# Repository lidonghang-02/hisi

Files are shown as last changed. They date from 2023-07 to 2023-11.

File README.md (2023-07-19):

# **猫咪自动铲屎机**
---
# 主体结构设计

主要分为三大部分，物联网部分、外壳设计、功能设计。

## 功能设计

不同于传统旋转式猫咪铲屎机，我们大胆采用了直线式铲屎。传统猫咪铲屎机，为旋转式铲屎，利用滚筒和网筛选出猫砂，再让猫屎自由落体进入容器中。这种结构可以说相当精妙，但这也使得清洁和处理猫砂成为一个问题。使得这种自动成为另一种负担。

而直线式可以有效解决这一问题。正如远距离传电由交流转为直流一般，大道至简。直线式，可将底部容器分为两个部分，一个装排泄物，一个装废弃的猫砂。并且可以方便的套上垃圾袋，方便铲屎官。

直线式并非完美无缺，这对于电机扭矩有极大的要求。因此我们特意选择了步进电机作为驱动装置，并且配合限位开关来限制步进电机的移动距离。然而这带来了另一个问题，即速度慢。经过我们深入研究Hi3861的硬件，我们选择Hi3861的硬件定时器，基于寄存器与内核代码重构硬件定时器代码，实现了us级脉冲，以此来驱动步进电机的高速运转。并且将其完善，使得其可以同STM32般简单易用，大大方便后续开发者，我们将其命名为“EasyTimer”。

当然，对于猫咪铲屎机，防夹猫也是一项必不可少的功能。每个铲屎官都害怕铲屎机会对可爱的猫主子造成伤害。因此，我们使用超声波测距来检测猫主子，当超声波的检测距离小于事先设定的阈值时，说明猫咪在铲屎机中;反之，则猫咪不在。

同时，超声波检测的距离变化也是我们铲屎的信号之一，其与压力模块的检测数据相结合来构成我们的铲屎信号。 我们通过测定重量的变化值来确定设备的工作状态以及排泄物重量。

对于一个设备没有UI是万万不可的，因此我使用OLED显示一些相关信息，供铲屎官了解。

此外，为了方便铲屎官对猫咪自动铲屎机的使用，我们开发了一个APP来实时监测猫咪自动铲屎机的工作状态和相关信息，让铲屎官在手机上就可以操控铲屎机。

## 物联网
在物联网方面，我们使用了华为云的IoT物联网中的设备接入IoTDA。通过MQTT协议与华为云IoT连接，并实时上传剩余猫砂重量，铲掉的排泄物重量等信息。

此外，我们开发了一个APP通过华为云IoT的API读取上传的数据，来实时监控铲屎机的工作状况和信息，并且可以通过发送指令，来控制铲屎机。该APP连接华为云，设备则通过MQTT连接华为云，实时发送数据和接受指令，并执行指令。

同时我们设计wifi配网功能，在启动时会自动读取nv工厂区的wifi配置，如果没有发现wifi，则进入AP配网模式。手机连接设备的热点后，发送wifi的ssid和密码即可配网。配网后会自动将相关配置写入nv工厂区，在下次启动时便会自动调用。

## 外壳设计



在外壳设计方面，我们始终贯彻方便铲屎官的理念。我们将铲屎机分为上下两个部分，上下都可拆卸，方便清洗。下面为分离的容器，上面则为猫砂盆，负责铲屎。



由于各种因素的影响，铲屎机的外壳对我们来说并不容易制造，因此我们仅在视频中展示了不成熟的结构演示。

与视频不同的是，我们将重力测量模块移到铲屎机的中部，位于猫砂盆底座的总部，并通过滑槽与滑块实现了猫砂盆底座与猫砂盆的分离与结合。为防止其意外脱落，我们还通过多种方式固定猫砂盆，但拆卸下来仅需四五步，十分方便。



更多的外壳细节，请自行查看3D模型。为方便查看，我们已经将其半剖视图制成PDF文件，并把各个部件导出为STL文件。

# 任务调度设计


众所周知HI3861是搭载有liteos的，因此为了压榨Hi3861的性能以及充分利用系统资源，我们抛弃了裸机定时器处理不同任务的方式，详细设计了任务调度。优先级从高到低分别为：电机驱动、传感器、按键检测、数据发送。其中电机为硬件定时器驱动的，因此在此不过多讨论。

裸机最大的问题就是单线程处理任务，因此在一些中大型项目甚至一些小型项目中会出现任务阻塞。导致整个设备运行阻塞，甚至瘫痪。我们便针对这种情况，不断进行设计和调试，便形成了如上图的任务调度。

传感器是防夹猫的关键，为保证猫主子的安全，我们将其置于优先级第一位。按键检测，对于时序要求也是相当高的，因此我们置于第二位，数据接受则置于最后。

# 功能说明

## UI界面显示

在OLED上，我们总共显示了三个参数，分别是：剩余猫砂重量、铲屎重量、铲屎次数。通过这三个参数，铲屎官可以了解猫咪的排泄状况以及添加猫砂的时间。

## 按键操作

为了方便操作，我们同时还设计了按键系统，通过按键的单击、双击、三击、长按，即可操控设备的运转。

长按是进入配网模式，如果已经连接wifi则不会进入。

双击是重新初始化重力感应模块，这需要在没有猫砂的时候进行，这样可以消除误差。

三击，打开舵机，使猫砂流入下方容器，方便更换猫砂。

## APP

可以远程监控设备数据，包括：铲屎重量，以及剩余猫砂重量。

同时配备铲屎的指令，一键即可开始工作。

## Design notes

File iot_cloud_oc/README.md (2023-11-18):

# 使用华为云IOT平台，代码依据使用BearPi-HM_Nano开发板智慧农业案例修改

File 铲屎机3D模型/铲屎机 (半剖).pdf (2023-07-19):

setPageBoxes("Crop", 0, 0, [0,2000,2000,0]);
标题零件代号 | 铲屎机 修订号 设计者 | Selcon 工程师 注释

本文档中的信息和/或材料均属作者所有，具有机密性。未经 书面授权，任何人不得使用、转载、出版或公开这些信息。 这些信息只能用于本文档中指定的制造业项目。

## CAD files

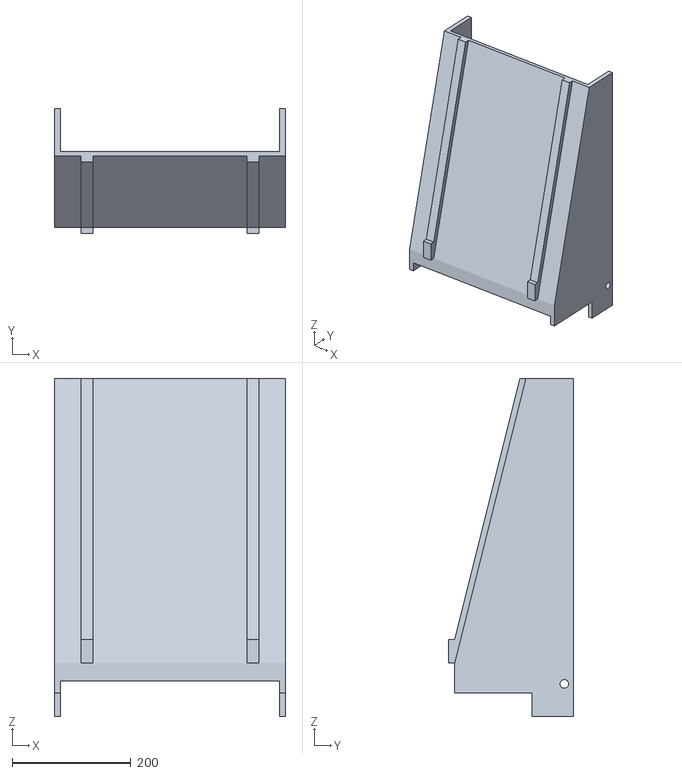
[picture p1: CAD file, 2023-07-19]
铲屎机3D模型/STL/猫砂盆.stl
390.0 x 210.0 x 570.0

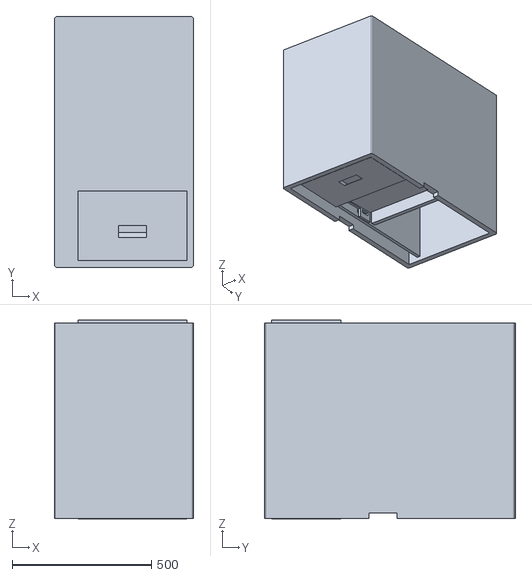
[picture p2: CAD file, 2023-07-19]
铲屎机3D模型/STL/铲屎机.stl
500.0 x 900.0 x 712.0

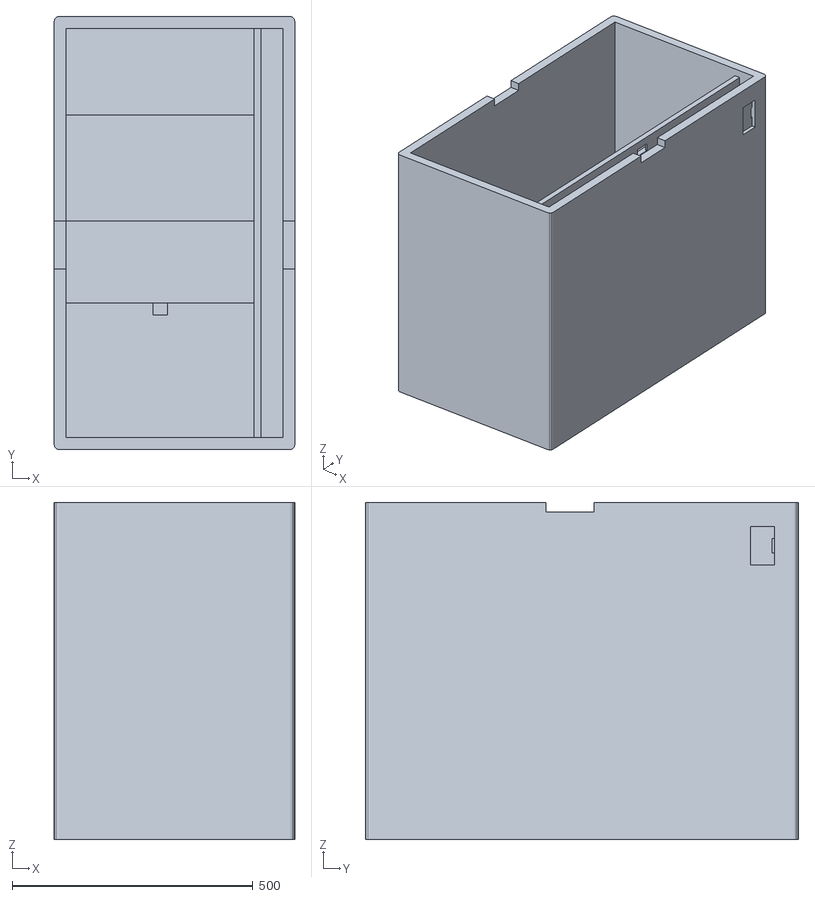
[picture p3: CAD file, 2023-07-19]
铲屎机3D模型/STL/外壳.stl
500.0 x 900.0 x 700.0

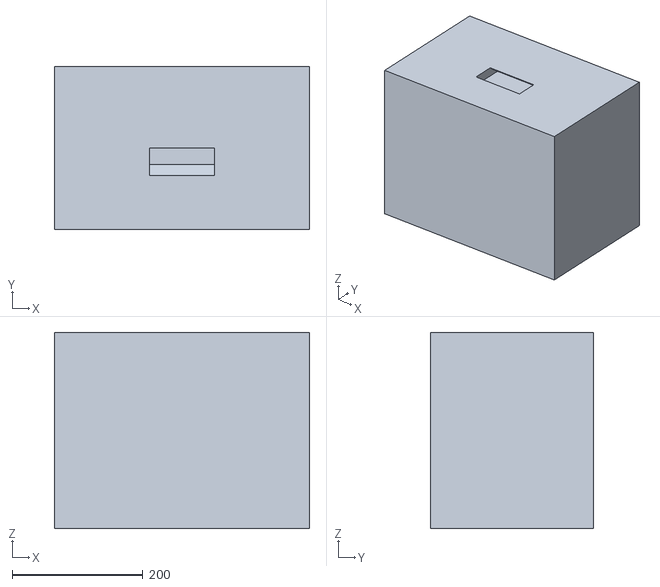
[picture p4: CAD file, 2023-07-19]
铲屎机3D模型/STL/容器.stl
390.0 x 250.0 x 300.0

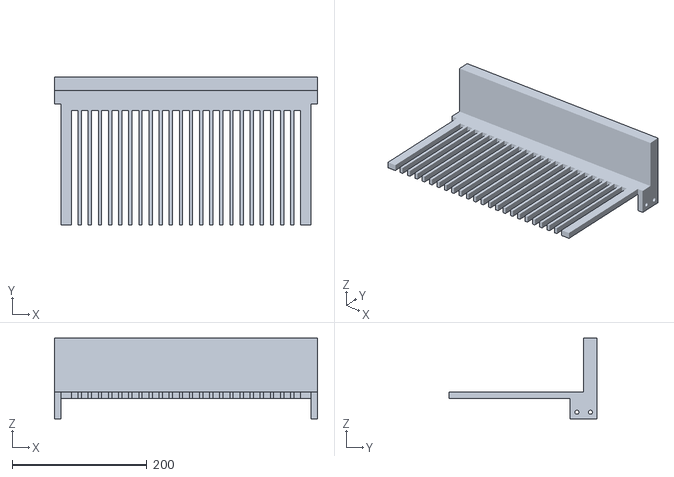
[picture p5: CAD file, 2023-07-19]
铲屎机3D模型/STL/猫铲.stl
390.0 x 220.0 x 120.0

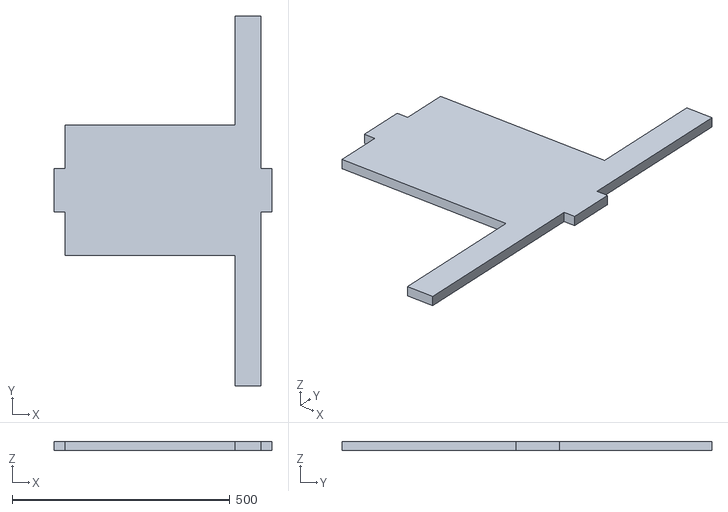
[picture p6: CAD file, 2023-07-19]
铲屎机3D模型/STL/外壳挡板.stl
500.0 x 850.0 x 20.0

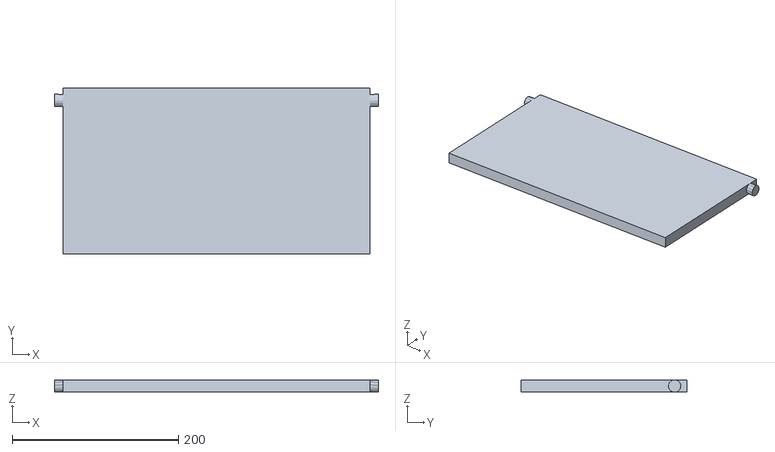
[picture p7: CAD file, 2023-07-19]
铲屎机3D模型/STL/挡板.stl
390.0 x 200.0 x 15.0

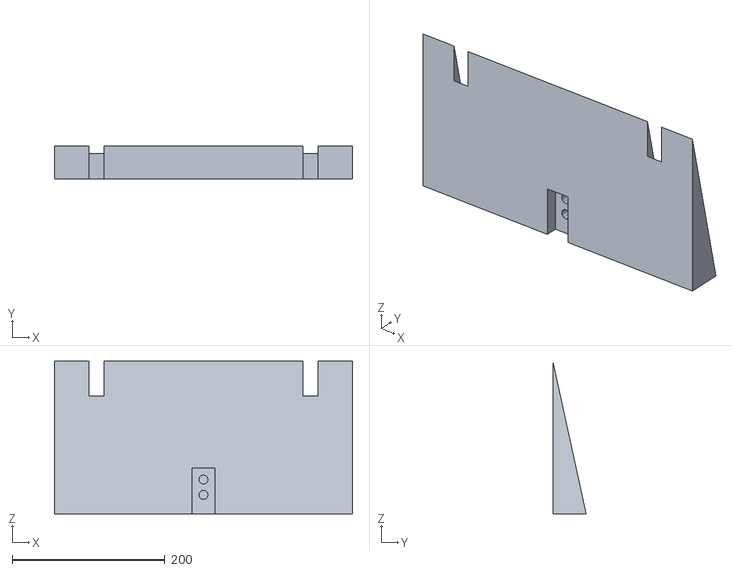
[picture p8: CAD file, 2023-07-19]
铲屎机3D模型/STL/猫砂盆底座.stl
390.0 x 43.6 x 200.0

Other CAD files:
铲屎机3D模型/外壳.ipt
铲屎机3D模型/外壳挡板.ipt
铲屎机3D模型/容器.ipt
铲屎机3D模型/挡板.ipt
铲屎机3D模型/猫砂盆.ipt
铲屎机3D模型/猫砂盆底座.ipt
铲屎机3D模型/猫铲.ipt
铲屎机3D模型/铲屎机.iam

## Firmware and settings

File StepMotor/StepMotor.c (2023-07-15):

#include "StepMotor.h"
#include "EasyTimer.h"
#include "EasyIsr.h"
#include "cmsis_os2.h"
#include <stdlib.h>
#include "LitterCleaner.h"

// #define Speed_Max

osTimerId_t Timer_ID = 0;
int8_t direction = 0;
Typedef_EasyTimerInit StepMotor_Timer = {0};
Typedef_EasyIsrInit StepMotor_Isr = {0};

/**
 * @brief 初始化电机IO口
 *
 * @param StepMotor_Pin 所要初始化的IO
 */
void StepMotor_InitPin(uint8_t StepMotor_Pin, uint8_t StepMotor_PinFunc)
{
    IoTGpioInit(StepMotor_Pin);
    IoTGpioSetFunc(StepMotor_Pin, StepMotor_PinFunc);
    IoTGpioSetDir(StepMotor_Pin, IOT_GPIO_DIR_OUT);
}

void StepMotor_CallbackFunc(void)
{
    static int8_t count = 0;

    StepMotor_SetStatus(count);

    if (direction == Positive)
    {
        if (++count >= 8)
            count = 0;
    }
    else if (direction == Negative)
    {
        if (--count < 0)
            count = 7;
    }

    // printf("Get into the IT, count = %d\n", count);
    EasyTimer_ClearIsrFlag(&StepMotor_Timer);
}

// void StepMotor_ControlCallbackFunc(void)
// {
// }

void StepMotor_PinInit(void)
{
    // Gpio set high level
    StepMotorPin_OFF;

    // Init Gpio
    StepMotor_InitPin(StepMotor_PinA, StepMotor_PinAFunc);
    StepMotor_InitPin(StepMotor_PinB, StepMotor_PinBFunc);
    StepMotor_InitPin(StepMotor_PinC, StepMotor_PinCFunc);
    StepMotor_InitPin(StepMotor_PinD, StepMotor_PinDFunc);
}

void StepMotor_PinDeInit(void)
{
    StepMotorPin_ON;
    IoTGpioDeinit(StepMotor_PinA);
    IoTGpioDeinit(StepMotor_PinB);
    IoTGpioDeinit(StepMotor_PinC);
    IoTGpioDeinit(StepMotor_PinD);
    
}

/**
 * @brief 电机初始化，包括IO和定时器
 *
 */
void StepMotor_Init(void)
{
    // initialize hardware timer to control the operation of step motor
    StepMotor_Timer.DEVICE = TIMER2;
    StepMotor_Timer.ITMASK = ITMASK_DISABLE;
    StepMotor_Timer.LOAD = EasyTimer_GetClockFreq();
    StepMotor_Timer.MODE = MODE_CYCLE;
    StepMotor_Timer.NVIC = NVIC_DISABLE;

    EasyHi_Error ack = EasyTimer_Init(&StepMotor_Timer);
    if (ack != EasyHi_SUCCESS)
        printf("Timer Error:%d\n", ack);
    else
        printf("StepMotor Timer Init Successfully!\n");

    // initialize the interrupt of hardware timer
    StepMotor_Isr.CALLBACKFUNC = StepMotor_CallbackFunc;
    StepMotor_Isr.CALLBACKPARA = NULL;
    StepMotor_Isr.DEVICE = TIMER_2_IRQ;
    StepMotor_Isr.PRIORITY = 7;

    ack = EasyIsr_Init(&StepMotor_Isr);
    if (ack != EasyHi_SUCCESS)
        printf("Isr Error:%d\n", ack);
    else
        printf("StepMotor Isr Init Successfully!\n");

    // // initialize the osTimer to control the speed of step motor
    // Timer_ID = osTimerNew(StepMotor_ControlCallbackFunc, osTimerPeriodic, NULL, NULL);
    // if (Timer_ID == NULL)
    //     printf("osTimer Init Fail\n");
    // else
    //     printf("osTimer Init Successfully\n");
}

void StepMotor_SetStatus(uint8_t motor_status)
{
    switch (motor_status)
    {
    case 0:
        StepMotorPin_OFF;
        StepMotorPinA_ON;
        break;
    case 1:
        StepMotorPin_OFF;
        StepMotorPinA_ON;
        StepMotorPinB_ON;
        break;
    case 2:
        StepMotorPin_OFF;
        StepMotorPinB_ON;
        break;
    case 3:
        StepMotorPin_OFF;
        StepMotorPinB_ON;
        StepMotorPinC_ON;
        break;
    case 4:
        StepMotorPin_OFF;
        StepMotorPinC_ON;
        break;
    case 5:
        StepMotorPin_OFF;
        StepMotorPinC_ON;
        StepMotorPinD_ON;
        break;
    case 6:
        StepMotorPin_OFF;
        StepMotorPinD_ON;
        break;
    case 7:
        StepMotorPin_OFF;
        StepMotorPinD_ON;
        StepMotorPinA_ON;
        break;
    default:
        printf("[StepMotor]Wrong Status!\n");
        break;
    }
    // printf("StepMotor_Status = %d\n", motor_status);
}

void StepMotor_SetSpeed(uint32_t cycle, int8_t direct)
{
    StepMotor_Timer.LOAD = cycle;
    EasyTimer_SetLoad(&StepMotor_Timer);
    direction = direct;
}

void StepMotor_Run(MotorStatus status)
{
    switch (status)
    {
    case FOR:
        osTimerStop(KeyTimer_ID);
        StepMotor_PinInit();
        StepMotor_SetSpeed(40000, Positive);
        EasyTimer_Start(&StepMotor_Timer);
        EasyIsr_Start(&StepMotor_Isr);
        printf("Motor Run Positive\n");
        break;
    case REW:
        StepMotor_SetSpeed(40000, Negative);
        EasyTimer_Start(&StepMotor_Timer);
        EasyIsr_Start(&StepMotor_Isr);
        printf("Motor Run Negative\n");
        break;
    case OFF:
        StepMotor_PinDeInit();
        EasyIsr_Stop(&StepMotor_Isr);
        EasyTimer_Stop(&StepMotor_Timer);
        Key_PinInit();
        osTimerStart(KeyTimer_ID, 1);
        printf("OFF\n");
        break;
    default:
        break;
    }
}

void StepMotor_Test(void)
{
    if (EasyTimer_Start(&StepMotor_Timer) != EasyHi_SUCCESS)
        printf("Timer Start Fail\n");
    if (EasyIsr_Start(&StepMotor_Isr) != EasyHi_SUCCESS)
        printf("Isr Start Fail\n");
}

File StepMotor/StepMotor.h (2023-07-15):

#ifndef __STEPMOTOR_H__
#define __STEPMOTOR_H__

#include "iot_gpio.h"
#include "iot_gpio_ex.h"
#include "cmsis_os2.h"
#include "stdio.h"
#include "unistd.h"


#define Positive (1)
#define Negative (-1)

// 定义步进电机IO端口及其复用
#define StepMotor_PinA  5
#define StepMotor_PinB  6
#define StepMotor_PinC  9
#define StepMotor_PinD  11
#define StepMotor_PinAFunc  IOT_GPIO_FUNC_GPIO_5_GPIO
#define StepMotor_PinBFunc  IOT_GPIO_FUNC_GPIO_6_GPIO
#define StepMotor_PinCFunc  IOT_GPIO_FUNC_GPIO_9_GPIO
#define StepMotor_PinDFunc  IOT_GPIO_FUNC_GPIO_11_GPIO

// 单独开启步进电机某相的信号
#define StepMotorPinA_ON IoTGpioSetOutputVal(StepMotor_PinA, IOT_GPIO_VALUE0)
#define StepMotorPinB_ON IoTGpioSetOutputVal(StepMotor_PinB, IOT_GPIO_VALUE0)
#define StepMotorPinC_ON IoTGpioSetOutputVal(StepMotor_PinC, IOT_GPIO_VALUE0)
#define StepMotorPinD_ON IoTGpioSetOutputVal(StepMotor_PinD, IOT_GPIO_VALUE0)

#define StepMotorPinA_OFF IoTGpioSetOutputVal(StepMotor_PinA, IOT_GPIO_VALUE1)
#define StepMotorPinB_OFF IoTGpioSetOutputVal(StepMotor_PinB, IOT_GPIO_VALUE1)
#define StepMotorPinC_OFF IoTGpioSetOutputVal(StepMotor_PinC, IOT_GPIO_VALUE1)
#define StepMotorPinD_OFF IoTGpioSetOutputVal(StepMotor_PinD, IOT_GPIO_VALUE1)

typedef enum
{
    FOR = 0,
    REW = 1,
    OFF
} MotorStatus;

// 关闭步进电机的输入信号
#define StepMotorPin_OFF do{    \
IoTGpioSetOutputVal(StepMotor_PinA, IOT_GPIO_VALUE1);   \
IoTGpioSetOutputVal(StepMotor_PinB, IOT_GPIO_VALUE1);   \
IoTGpioSetOutputVal(StepMotor_PinC, IOT_GPIO_VALUE1);   \
IoTGpioSetOutputVal(StepMotor_PinD, IOT_GPIO_VALUE1);   \
}while(0)

#define StepMotorPin_ON do{    \
IoTGpioSetOutputVal(StepMotor_PinA, IOT_GPIO_VALUE0);   \
IoTGpioSetOutputVal(StepMotor_PinB, IOT_GPIO_VALUE0);   \
IoTGpioSetOutputVal(StepMotor_PinC, IOT_GPIO_VALUE0);   \
IoTGpioSetOutputVal(StepMotor_PinD, IOT_GPIO_VALUE0);   \
}while(0)

void StepMotor_Init(void);
void StepMotor_SetStatus(uint8_t motor_status);
void StepMotor_InitPin(uint8_t StepMotor_Pin, uint8_t StepMotor_PinFunc);
void StepMotor_Test(void);
void StepMotor_Run(MotorStatus status);
void StepMotor_PinDeInit(void);
void StepMotor_PinInit(void);

#endif

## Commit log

2023-07-12 add function to drive motor and updata tasks to deal with information
2023-07-14 add cat scoop 3D model
    [猫铲.0001.ipt, 猫铲.ipt, 猫铲.stl]
2023-07-14 rebuild the thread construction and fix error
    [EasyTimer.h, HCSR04.c, LitterCleaner.c]
2023-07-15 update oled
    [猫铲.0001.ipt, 猫铲.ipt, 猫铲.stl]
2023-07-15 fix a lot of bug
    [HCSR04.c, LitterCleaner.c, SteeringEngine.c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]
2023-07-18 fix error and update README
    [LitterCleaner.c]
2023-07-19 update 3D models
    [外壳.ipt, 外壳.stl, 外壳挡板.ipt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]
2023-07-19 make some adjustments to models
    [外壳.ipt, 外壳.stl, 猫砂盆.ipt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]
